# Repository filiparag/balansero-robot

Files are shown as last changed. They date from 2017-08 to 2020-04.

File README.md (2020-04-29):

## Modeling, simulation and hardware implementation of a self-balancing robot

The aim of this paper is modeling, simulation and implementation of a self-balancing robot. The
problem of a self-balancing robot is considered as a problem of inverted pendulum stabilisation,
while a DC motor is used as the drive motor.

Deflection angle indicates the angle by which is the robot inclined to a side, in other words, by how
many degrees is the y-axis of the robot rotated from the absolute y-axis, so that the center of wheels
is exactly at the section of these axises.

In simulation, the deflection angle is measured in four ways: using a gyroscope, an accelerometer,
both gyroscope and accelerometer in combination using a complementary filter and both gyroscope
and accelerometer in combination using Kalman filter. These sensors are placed on the apex of the
robot in order to maximise the amplitude of measured values. Two types of stabilisation controllers
are used: PID and LQR. Respective performance of these regulators are compared relative to the
way that the angle is obtained.

Results of the simulation in which only a gyroscope is used indicate that this sensor accumulates
measuring error exceptionally fast, which results in a value over after just one second. Because
of this, stabilisation is not possible regardless of the regulator.
In the case of measuring using an accelerometer, a constant measuring error is observed and that the
presence of noise is more apparent than when a filter is used. Furthermore, noise’s amplitude is
greater with LQR regulator as a consequence of flickering noise, which is expected because the
current deflection angle changes at a quicker rate using PID. Contrary to LQR, stabilisation using
PID regulator has overshoot.

When a complementary filter is used, the gyroscope error accumulation is not observed and both
constant error and noise of an accelerometer are less pronounced. Similarly to previous case, noise
is more apparent with LQR, but overall noise is lower.
When Kalman filter is used, properties of the error and noise are similar to those from
complementary filter, except that the noise is of less amplitude. Regardless of the regulator type,
stabilisation is achieved with the lowest noise of all four cases. Noise is again lower when LQR
regulator is used due to the flickering noise.
All simulation hypotheses set during the initial problem analysis and modeling are confirmed: robot
can successfully stabilise regardless of regulator type, except when measurements are only acquired
from a gyroscope.

Unlike in simulation, PID regulator is only implemented in hardware where the measurements
represent output of a complementary filter of both gyroscope and accelerometer. Major setback in
hardware system emerged as a significant free movement in transfer of the motor torque to the
wheel axle; as a consequence, the robot can be displaced from balance and disable any further
stabilisation. The system is successfully put into stable oscillatory movement, but the stabilisation is
not possible and the hypothesis is not confirmed.
To review the plausibility of this hypothesis, further work should focus on removing the free
movement in mechanical transfer. Also, stabilisator performance should be observed when the
center of robot’s mass is shifted downwards, in other words, when additional weight is added to its
base.

## Modeliranje, simulacija i implementacija samobalansirajućeg robota

Cilj ovog rada je modeliranje, simulacija i izrada samobalansirajućeg robota.

Samobalansirajući
robot je mehanički sistem za kretanje po ravnim površinama sa kojima je u kontaktu preko para
točkova na jednoj osovini. Osnovna funkcionalnost ovakvog robota je samostalno održavanje centra
mase iznad ose rotacije.

Problem stabilizacije posmatran je kao problem stabilizacije inverznog fizičkog klatna, dok je kao
pogonski motor korišćen DC motor. U simulaciji, ugao otklona robota od pravca gravitacije, meren
je na četiri različita načina: pomoću žiroskopa, pomoću akcelerometra, pomoću žiroskopa i
akcelerometra zajedno u kombinaciji sa komplementarnim filterom i pomoću žiroskopa i
akcelerometra zajedno u kombinaciji sa Kalmanovim filterom.

U hardverskoj implementaciji korišćeni su žiroskop i akcelerometar u kombinaciji sa
komplemetarnim filterom. U simulaciji su korišćene dve vrste stabilizatora: PID i LQR, dok je u
hardveru implementiran samo PID regulator. Poređene su performanse stabilizacije sa ovim
stabilizatorima u odnosu na način estimacije ugla.

U simulaciji dobijeno je da je stabilizacija nemoguća ukoliko se koristi samo žiroskop, dok je
stabilizacija u ostalim slučajevima moguća. Najbolje performanse su dobijene ako se ugao otklona
meri pomoću žiroskopa i akcelerometra zajedno u kombinaciji sa Kalmanovim filterom. U hardveru
nije bilo moguće izvršiti potpunu stabilizaciju sistema zbog velikog slobodnog hoda motora jer bi se
robot stalno izvodio iz ravnotežnog položaja.

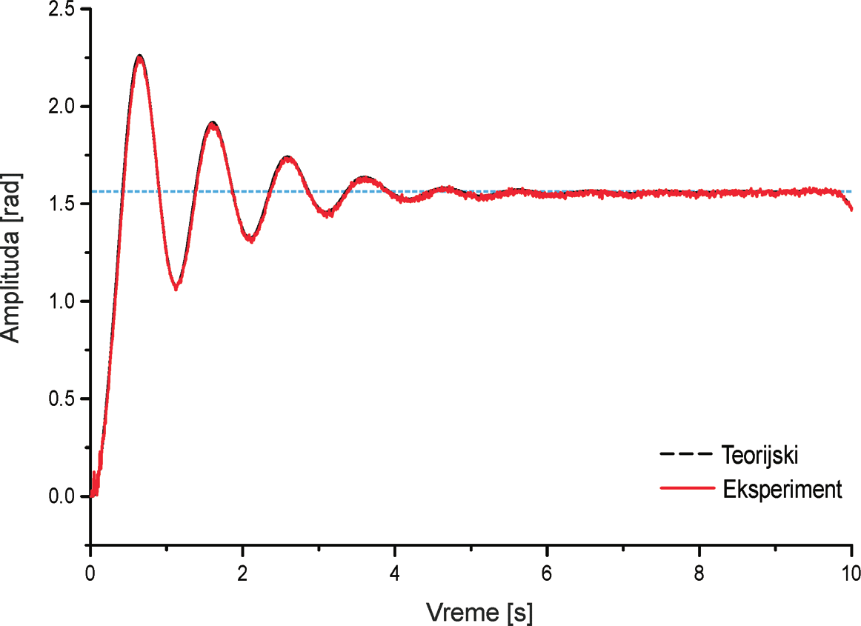
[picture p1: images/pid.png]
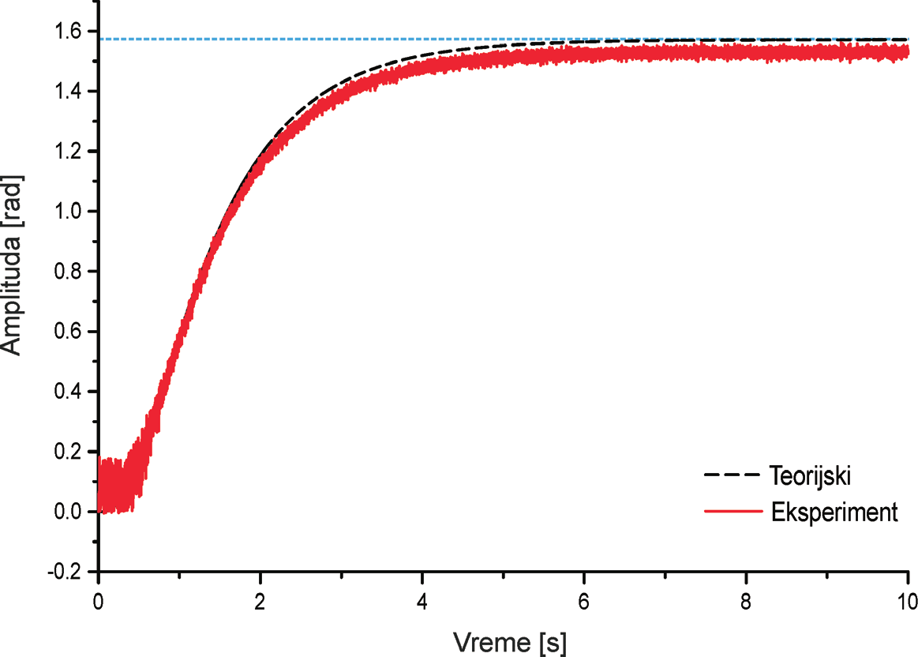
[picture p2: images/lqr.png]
lqr
|  |  |
| -- | -- |
| Robot deflection as a function of time using PID controller and complementary filter inside the simulation | Robot deflection as a function of time using LQR controller and complementary filter inside the simulation |
| Zavisnost nagiba robota od vremena sa PID regulatorom i komplementarnim filtrom u simulaciji | Zavisnost nagiba robota od vremena sa LQR regulatorom i komplementarnim filtrom u simulaciji |

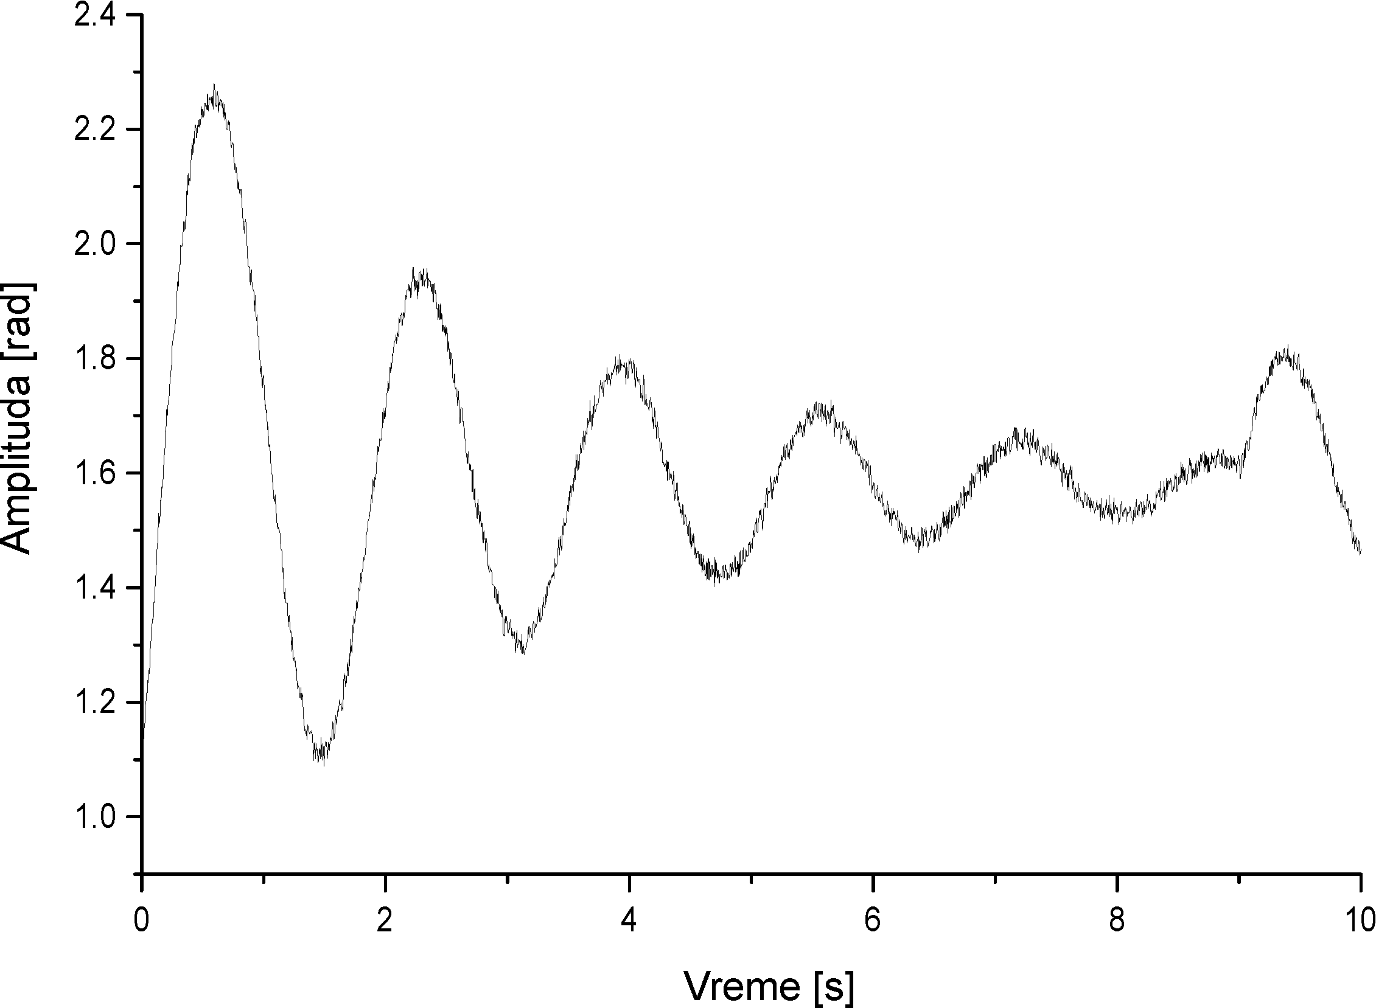
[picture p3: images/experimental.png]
experimental
|  |
| -- |
| Robot deflection as a function of time using PID controller and Kalman filter |
| Zavisnost nagiba robota od vremena sa PID regulatorom i komplementarnim filtrom |

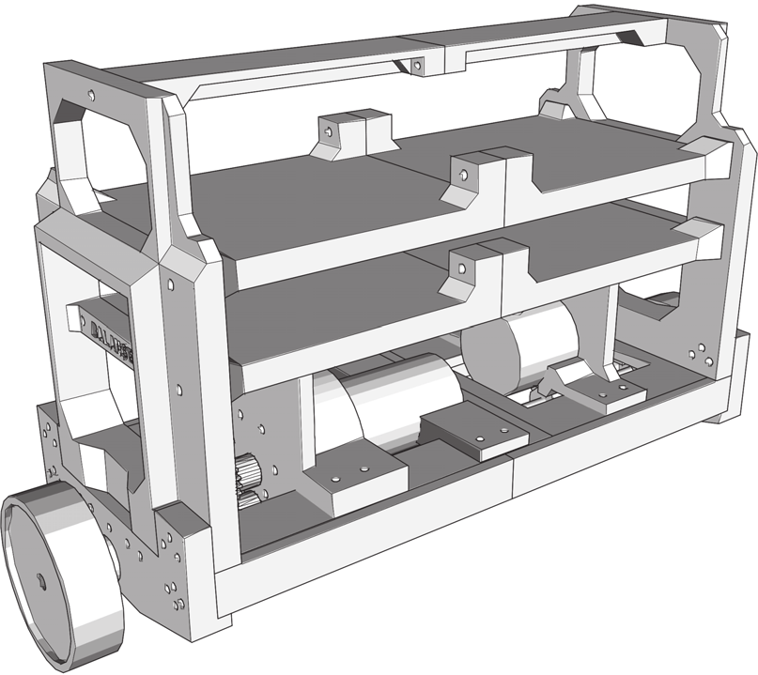
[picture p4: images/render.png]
|  | 
| -- |
| 3D render of the assembled robot |
| 3D prikaz sklopljenog robota |

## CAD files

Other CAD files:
Model/Balansero.skp
Model/Model.skp

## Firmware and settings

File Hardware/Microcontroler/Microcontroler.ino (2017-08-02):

enum  dimension {X, Y, Z};

<<<<<<< HEAD
double reference = -0.4;
double angle = 0;

double Kp = 0; //15.25
double Kd = 0; //13.51
=======
double reference = -0.65;
double angle = 0;

double Kp = 8;
double Kd = 0;
>>>>>>> 10adec8d5e922443e36e502a7df369fb13f4d6fb
double Ki = 0;
double range = 1; //Ako je range = 0, koeficijenti mogu da idu od 0 do 5

double error = 0;
double last_error = 0;
double derror = 0;
double ierror = 0;
double u = 0;

int Pin_PWM = 9;
int Pin_DIR = 8;

bool manual_pid = true;

namespace IMU {

char  imu_buffer[32];
short imu_buffer_end = -1;

bool new_measurement = false;

struct Values {
  double X, Y, Z;
} Values;

void parse_buffer () {

  imu_buffer_end -= 3;

  short comma1 = -1,
        comma2 = -1;

  for (short it = 0; it <= imu_buffer_end; ++it) {
    if (imu_buffer[it] == ',') {
      if (comma1 == -1) {
        comma1 = it;
      } else {
        comma2 = it;
      }
    }
  }

  char  buffer_x[comma1],
        buffer_y[comma2 - comma1 - 1],
        buffer_z[imu_buffer_end - comma2];

  for (short it = 0; it < comma1; ++it)
    buffer_x[it] = imu_buffer[it];

  for (short it = 0; it < comma2 - comma1 - 1; ++it)
    buffer_y[it] = imu_buffer[comma1 + 1 + it];

  for (short it = 0; it <= imu_buffer_end - comma2; ++it)
    buffer_z[it] = imu_buffer[comma2 + 1 + it];

  Values.X = atof(buffer_x);
  Values.Y = atof(buffer_y);
  Values.Z = atof(buffer_z);

  new_measurement = true;
}

void  buffer_add (char c) {

  if (c != '#' && c != 'Y' && c != 'P' && c != 'R' && c != '/n') {
    if (c == '=') {
      parse_buffer();
      imu_buffer_end = 0;
    } else if (imu_buffer_end > -1) {
      imu_buffer[imu_buffer_end] = c;
      ++imu_buffer_end;
    }
  }
}

double read_value (dimension d) {

  new_measurement = false;

  switch (d) {
    case X:
      return Values.X;
    case Y:
      return Values.Y;
    case Z:
      return Values.Z;
  }

}

}

void setup () {
  
  Serial.begin(57600);
  pinMode(Pin_PWM, OUTPUT);
  pinMode(Pin_DIR, OUTPUT);

  if (manual_pid) {
      Kp = analogRead(A3) / 886.0 * 30.0;
      Kd = analogRead(A1) / 886.0 * 50.0;
//      Serial.println(Kp);
  }
  
}

void loop () {

  if (Serial.available() > 0)
    IMU::buffer_add(Serial.read());

  if (IMU::new_measurement) {
    
    angle = IMU::read_value(Z);

//        Serial.println(angle);



     Kp = analogRead(A3) / 886.0 * 30;
     Kd = analogRead(A1) / 886.0 * 50;

    error = reference - angle;
    derror = error - last_error;
    ierror = ierror + error;
    u = error * Kp + derror * Kd + ierror * Ki;
    Motor(round(u));
    last_error = error;
  }
}

void Motor(int input)
{
  int voltage = input;
  int dir = 0;

  if (input > 0) dir = 0;
  if (input < 0) dir = 1;
  if (input > 255) voltage = 255;
  if (input < -255) voltage = -255;

  voltage = abs(voltage);

  analogWrite(Pin_PWM, voltage);
  digitalWrite(Pin_DIR, dir);

<<<<<<< HEAD
  Serial.print(angle);
  Serial.print(',');
  Serial.print(voltage);
  Serial.print(',');
  Serial.print(Kd);
  Serial.print(',');
  Serial.println(Kp);
  
=======
      Serial.print(angle);
      Serial.print(',');
      Serial.print(Kp);
      Serial.print(',');
      Serial.print(Kd);
      Serial.print(',');
      Serial.println(u);
>>>>>>> 10adec8d5e922443e36e502a7df369fb13f4d6fb
}

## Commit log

2017-07-21 Complementary filter
2017-07-22 Motor model
    [DC_Motor_2.STL]
2017-07-22 Sensors fix
2017-07-22 Update 22.07 12.49
    [Model.skp]
2017-07-22 Motor converted format
    [DC_Motor_2.STL]
2017-07-22 Motor STL
    [DC_Motor_2.STL]
2017-07-22 Motor and encoder
    [Model.skp]
2017-07-23 Model motor fix
2017-07-25 Dodat PID
2017-07-25 Kalman filter algorithm
2017-07-25 Kalman filter
2017-07-26 IMU Kalman [Unfinished]
2017-07-26 Kalman IMU test script
2017-07-27 call Kalman from Sensors.m
